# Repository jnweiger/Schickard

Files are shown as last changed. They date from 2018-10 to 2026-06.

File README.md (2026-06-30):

# Schickard
Lasercut reconstruction of the first calculating machine designed by Wilhelm Schickard 1623. 

Published at https://www.thingiverse.com/thing:3451695

Presented at
* <A href="https://www.facebook.com/pg/hackmake.de/events/">Hack-n-Make 2018</a>
* <A href="https://harenberg-maker.de/mmf-nuernberg-2019/">Mini Maker Faire Nürnberg (26. Jan 2019)</A>
* <a href="https://youtu.be/ot1D30ZgLgg">Make Munich 2019</a>
* <A HREF="http://www.VCFe.org/" TITLE="VCFe 20.0 am 27./28.April 2019 in München">VCFe 20.0 am 27./28.April 2019 in München VCFe 20.0 in München</A>
* <a href="http://www.faerdderla.de/events/modellbaunetzwerk-franken-5-modellbau-ausstellung-2/">5. Modellbau Ausstellung Franken (4./5. Mai 2019)</a>
* <a href="https://maker-faire.de/maker/die-schickardsche-rechenmaschine/">Maker Faire Berlin 2019 (17.-19.5.2019)</a>
* <a >Retrolution Hanau 2019</a>
* <a href="https://www.vcfb.de/2019/vortraege_workshops.html#schickard">Vintage Computer Festival Berlin 2019</a>
* <a href="https://www.lug-noris.de/lug-nuernberg/linux-presentation-day">Linux Presentation Day 2020.2</a>
* <a href="https://maischule.de/von-rechenmeistern-zur-rechenmaschine-eine-reise-in-die-vergangenheit-mit-juergen-weigert-vom-fab-lab-region-nuernberg-e-v">Maischule Fürth (10. Juli 2023)</a>
* <a href="https://meik.isc.schule/2026/06/15/schickardsche-rechenmaschine/">Industrieschule Chemnitz (15.6.2026)</a>

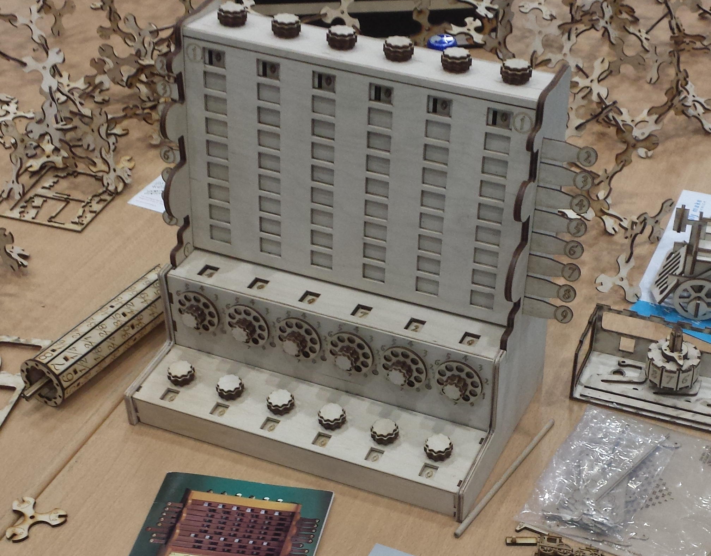
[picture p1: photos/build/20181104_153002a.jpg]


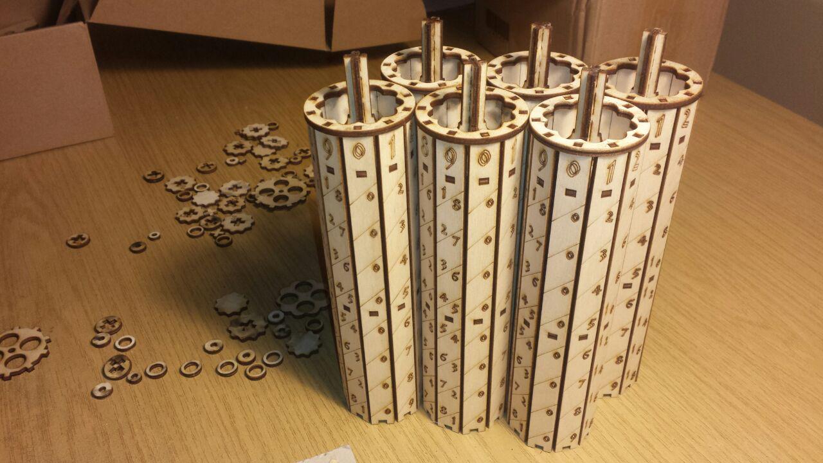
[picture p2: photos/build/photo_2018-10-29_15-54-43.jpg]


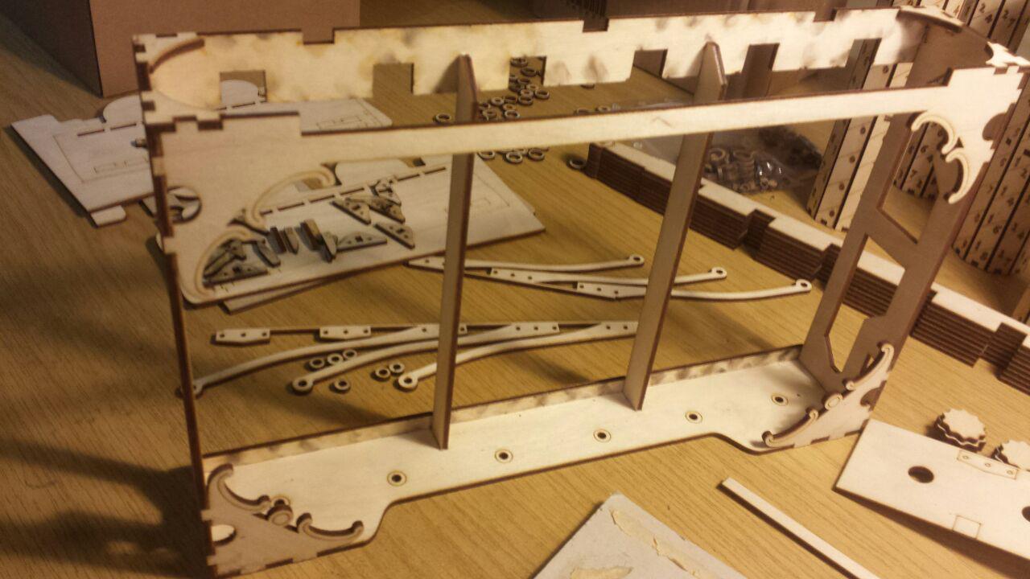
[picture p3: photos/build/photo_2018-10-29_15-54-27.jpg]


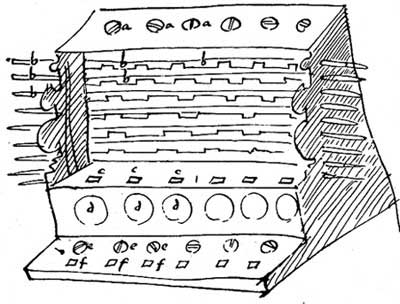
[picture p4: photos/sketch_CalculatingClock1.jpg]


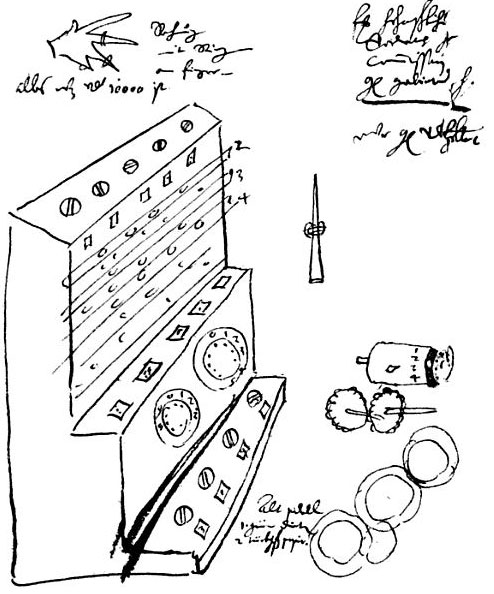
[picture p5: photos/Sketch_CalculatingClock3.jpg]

  
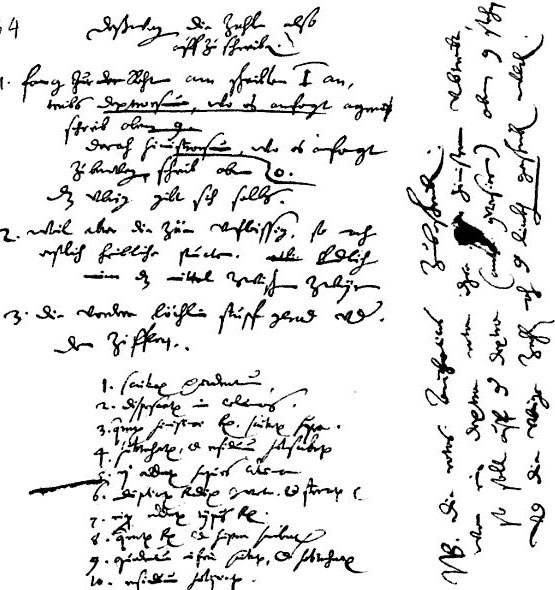
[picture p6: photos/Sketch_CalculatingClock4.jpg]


Video Clips:
* <a href="https://youtu.be/f-myRG2Cc5w">Test of the gear train</a>
* <a href="https://youtu.be/Xd8V1M9Gz_0">Adding 4+4+4+4 ...</a>
* <a href="https://youtu.be/RR3bb4ij2YE">Adding 753 + 296 = 1049</a>

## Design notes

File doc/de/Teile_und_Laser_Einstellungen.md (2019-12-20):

Beginne hier zu lesen.

Übersicht der Bauteile
======================

Die Teile der Maschine gliedern sich in fünf Gruppen:

* Speicherwerk (memory unit)
* Addierwerk (adder unit)
* Multiplikationswerk (napier unit)
* Seitenwände
* Übrige und optionale Teile

Die drei Werke und die Seitenwände sollten aus 3.2mm Birken-Sperrholz gefertigt werden.
Die Datei src/BOM.txt (billl of materials) listet alle benötigten Materialen.
Am wichtigsten davon sind drei Sperrholzplatten 76cm x 50cm. Aller lasergeschnittenen Teile
werden daraus gemacht.

Achte beim Holzeinkauf auf die exakte Dicke. Die Platten sollten maximal 3.2mm dick sein. Manche Hersteller verkaufen bis zu 3.5mm dicke Platten als 3mm (funktioniert hier nicht!). Manche Hersteller halten exakt 3.0mm ein (das funkioniert, baucht aber mehr Holzleim). Mit 3.2mm Holz funktionieren viele Verbindungen als stramme Steckverbindungen, die oft keinen Leim benötigen.
Birkensperrholz sollte in guter Qualität gekauft werden. Astfrei, glatt, absolut eben. Frage nach "Laserqualität". Mindestens handelsbezeichnung "BB/B".
Beim Zuschnitt muss die Holzmaserung in Längsrichtung verlaufen. (Holzfedern quer zur Maserung funktionieren nicht!)

Buchensperrholz ist auch eine gute Wahl. Es ist deutlich härter, aber auch teurer.
Billiges Pappelsperrholz sollte vermieden werden. Es ist zu weich für Zahnräder.

Die drei Dateien schickard_napiers.svg, schickard_adder.svg und schickard_memory.svg im Unterverzeichnis src ergeben die komplette Maschine. In jeder der Dateien sollte die Ebene 'laser' sichtbar sein. Dies ergibt einer 76cm x 50cm
Platte pro Datei.  Alle weiteren Dateien enthalten optionale Teile oder Hilfskonstruktionen aus denen die drei schickard_*.svg Dateien erzeugt wurden.

Im Folgenden wird beschrieben, was in den drei Platten enthalten ist. Die Teile sollten man streng nach Werken
sortiert werden. Du kannst die Platten nacheinander schneiden und zusammenbauen, wenn du dich an die Reihenfolge hier hältst. Das Multiplizierwerk (napier unit) wird zuletzt gebaut, da es die übrigbleibende Teile von den anderen Platten verwendet.

Speicherwerk
------------
Dieses Werk ist einfacher als die anderen, und sollte zuerst zusammengebaut werden.
Das Speicherwerk ist eine flache Kiste (ca. 33cm lang, 3cm hoch, 7cm tief) am unteren Ende der Maschine.
Auf der Oberseite sind sechs Drehknöpfe und sechs Fenster, die je eine Ziffer zeigen. Zu Beginn einer Multiplikation wird hier eine der beiden Zahlen durch die Drehknöpfe eingestellt.
Die Unterseite hat Aussparungen, um einen Blick in den Mechanismus zu erlauben.

Alle Teile des Speicherwerks finden auf der linken Hälfte der Datei schickard_memory.svg platz -- die rechte Hälfte enthält eine der Seitenwände und einige Teile des Multiplizierwerks.
Von einem Typ Ring sind 9 Exemplare vorhanden. Sechs davon werden für das Speicherwerk benötigt, drei gehören zum Multiplizierwerk.

Ausserdem befinden sich 13 Teile für Positionierhilfen auf der Platte, die nur während der Montage benutzt werden. Diese sind nicht Teil der Maschine.

 * Finde fünf kleine Rechtecke 32mm x 14mm mit gezahnten Aussparungen, die mit "Positioning Aid Knob Assembly" beschriftet sind. Weitere fünf dieser Teile sind unbeschriftet. (Nur je vier beschriftete und unbeschriftete werden benötigt. Falls eines verloren geht oder bricht, benutze das fünfte.)
 * Finde zwei gewinkelte Teile mit Innekurve ca. 6cm x 5cm mit der Beschriftung "Napier - Positioning Aid Side Connectors". Lege sie zur Seite, sie werden später bei den Seitenwänden benutzt.
 * Finde ein rechteckiges Teil ca. 7cm x 3cm mit der Beschriftung "Positioning Aid Side Connectors Memory". Lege es zur Seite, es wird später bei den Seitenwänden benutzt.

Addierwerk
----------
Das Addierwerk ist ein Kiste (ca. 33cm x 8cm x 8cm) in der Mitte der Maschine. Auf der Vorderseite sind sechs Räder mit Knöpfen. Jedes Rad hat 10 Löcher und kann mit einem 6mm Rundstab oder einem Stift bedient werden. Die Oberseite hat sechs Fensterchen, die das Rechenergebnis anzeigen.
Die  Kiste hat keinen Boden und die Rückseite ist durchbrochen, so dass der komplizierteste Teil der Maschine gut sichtbar ist: Das Räderwerk. Dieser Mechanismus dient dem Zehnerübertrag zur jeweils nächsten Stelle. [Wilhelm Schickard](https://en.wikipedia.org/wiki/Wilhelm_Schickard Wikipedia artikel über Wilhelm Schickard) war vermutlich der erste, der einen solchen Mechanismus konstruiert und gebaut hat.

Das Rechenergebnis wird in diesem Werk angezeigt. Um eine Multiplikation zu beginnen, sind die Räder so zu drehen, dass 000000 angezeigt wird.

Alle Teile passen in schickard_adder.svg und belegen etwa zwei Drittel einer Platte 76cm x 50cm. Das rechte Drittel dieser Datei enthält einen Satz Seitenwandteile und drei Sätze Kreuzwellen der Nepier-Walzen.

Ausserdem befinden sich 12 Teile für Positionierhilfen auf der Platte, die nur während der Montage benutzt werden. Diese sind nicht Teil der Maschine.

 * Finde fünf kleine Rechtecke 32mm x 14mm mit gezahnten Aussparungen, die mit "Positioning Aid Knob Assembly" beschriftet sind. Weitere fünf dieser Teile sind unbeschriftet. Es können statt dessen die Montagehilfen vom Speicherwerk auch hier verwendet werden. Dann werden diese 10 Teile nicht benötigt.
 * Finde zwei kleine Rechtecke ca. 11cm x 5cm, die mit "Positioning Aid Carry Wheels" beschriftet sind.

Alle Knöpfe sind gleich. Insgesamt werden 18 Stück benötigt.

Die Knöpfe des Addierwerks werden auf Lochscheiben montiert. Die Position der '0' ist mit einer kleinen Kerbe auf der Lochscheibe markiert.
Die Ziffernwalze wird aus einem verzahnten Ring, einer Scheibe und 10 Ziffernplätchen aufgebaut. Auf Ring und Scheibe ist die Position der '0' jeweils durch ein Rechteck markiert.
Die Wellen bestehen aus drei Teilen, die kreuzförmig verglebt werden. Es gibt zwei verschiedene Sätze Wellenteile, beschriftet "1, 100, 10.000" bzw. "10, 1.000, 100.000"
Alle Zahnräder und Abstandsquadrate werden von hinten auf die Wellen gesteckt. Die Schrift zeigt nach hinten.
Die grossen 10-Zähne-Räder haben die Position der '0' mit einem Strich markiert.

Die Reihenfolge der in der Teile auf die Wellen gesteckt werden, ist wie folgt:

3 Wellen "1, 100, 10.000":
  * erst 2x Einzahn,
  * dann 4x Abstandsquadrat,
  * dann 2x 10-Zähne-Rad aufstecken.

3 Wellen "10, 1.000, 100.000":
  * erst 2x 10-Zähne-Rad,
  * dann 4x Abstandsquadrat,
  * dann 2x Einzahn aufstecken.

Dabei sind die beiden Zahnstocherlöcher immer links. Mit den Zahnstochern
werden alle Teile genau ausgerichtet. Alle bis auf das letzte Teil werden ohne
Leim aufgesteckt, nur das letzte Teil und die beiden Zahnstocher werden
verklebt.

Die fünf Übertragswellen bestehen aus 6mm Buchenrundstäben, 90mm lang. Auf der
Rückwand sind sie mit A, B, C, D, E beschriftet.  Für bzw. A, C, E bzw. B, D
gibt es jeweils eine Montagehilfe "Positioning Aid Carry Wheels". Diese haben
passende Öffnungen für die Ringe und Räder.  Auch hier werden zwei Zahnstocher
zur genauen Ausrichtung montiert.  Mit dem letzten Ring wird die Welle in der
die Rückwand des Addierwerks befestigt, wie auf den Montagehilfe eingezeichnet.

Napier Unit
-----------
This is the upper part of the machine, where multiplications are done. It is named after [John Napier](https://en.wikipedia.org/wiki/John_Napier "Wikipedia Article on John Napier"), who invented the "[Napier's Bones](https://en.wikipedia.org/wiki/Napier%27s_bones)" giving the layout of the numbers on the drums.

The Napier unit consists of a box (ca. 33cm x 21cm x 6cm) with 6 drums standing upright. The back side of the box is open, to allow studying the interier,
the front has 8 sliders that can cover one row each of the multiplication table. Row "1" is always visible.
On the top are 6 knobs. To start multiplying, close all slides and enter one of the two numbers here by turing the knobs, so that it is shown in Row "1".

All parts for the box and most parts of the drums are in the schickard_napiers.svg file.
The layout fills one 76cm x 50 cm board. Two sets of napiers bones and several rings and shafts for the drums are
on the lower right hand side of the schickard_memory.svg. Three sets of shaft parts are on the right hand side
of schickard_adder.svg.

Side Walls
----------
The machine has a modular design. Each of the three units as its own enclosure. The left and right sides of the
machine are the two walls that hold the three modules in place. Each wall consits of two layer of plywood
 * the outer layer with only openings for the 8 slides,
 * the inner layer with openings for also the sides of the three units.

The memory unit is locked into the side walls using one connector on each side.
The napiers unit has two connectors (top and bottom) on each side.
The adder unit has none.

A wall connector is 30mm long, 6mm wide (two layers of plywood glued together), and in the middle 13mm high.
A rectanglar hole 4mm x 6mm goes across the connector.
Wall connectors are glued with their flat surface into the sidewalls. Their curved part extends into the sides of the memor or napier box. In this position a slim wedge can be inserted in to the hole of the connector locking the box in place.

Miscellaneous
-------------

The file schickard_misc_construction.svg has an additional set of rings (replacing the ones found in schickard_memory.svg). There are three different outer diameters 14.3mm, 14.4mm, and 14.5mm here. You can optionally cut these rings out of harder material like acrylic or kraftplex. The rings server as bearings for the shafts of napier and adder unit.

The file schickard_sign.svg has a wooden sign with two feet, for display with the machine. The sign is optional, it is not a part of the machine. This is designed for a 4mm plywood board.

There are also arrays of red lines, 90mm apart and 13mm apart. These can be used to cut the needed 4mm and 6mm
shafts from beech wood rods with a lasercutter.

Laser Settings
==============
To cut the parts from the boards you need access to a laser cutter with a bed of at least 76cm x 50cm size.
Find a machine large enough at your nearest FabLab or hacker space.
A machine with ca. 60-80 Watts is recommended. Expect ca. two hours cutting time and another two hours handling time
for collecting the parts from the machine and sort them into suitable containers. In total, there are ca. 600 parts.

The source files are are SVG format. These files can be processed with VisiCut (or converted with inkscape to PDF or other formats needed for your laser machine). Please re-check the dimensions (76 x 50) of the drawings after conversion.

The line colors (stroke or outline color) used in the SVG files have different meaning.

 * Red. These lines cut through the board. (E.g an 80W Thunderlaser may use speed 30, power 70/50 to cut through 3mm birchwood.)
 * Green. These lines are superficial markings. (E.g an 80W Thunderlaser may use speed 200, power 8/35 on birchwood.)
   Engraving mode (rasterization) may also work for green, but is not recommended, as it may be much slower.
 * Blue and other colors (if any) are to be ignored.

Several different fill colors were used during constructions, some parts have no fill.
These colors have no meaning for laser cutting.
Line width (stroke thickness) is typically 0.1 or 0.2mm. This also has no meaning for laser cutting.

Expect that some of the smaller parts may fall through the grid of the laser bed. It is recomended to clean any previous waste from the machine before starting. Most of the smaller parts come larger numbers than actually needed to save you from collecting each and every dropped piece.

A large table surface helps to keep the parts arranged into small piles. If needed, use containers like cardboard boxes or transparent zip bags for handling the parts between cutting and assembly.

Next steps
==========
Next read 'Adjustments and Maintenance' before assembly.
You learn there where to apply grease before a part becomes inaccessible.
Do not forget check out the assembly gallery in the photos folder before you start.

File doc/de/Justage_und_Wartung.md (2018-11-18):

Schmierung vor der Montage
==========================

Alle beweglichen Teile sollten mit Kerzenwachs eingerieben werden. Ein alter Kerzenstummel eignet 
sich gut dafür. Nimm Dir besonders Zeit, um

1) alle Flächen der kleinen Rollen an den Enden der Federn einzuwachsen.
2) alle Zähne von jedem Zahnrad einzuwachsen.

Die Schieber brauchen nur sehr wenig Schmierung. Sie dürfen etwas Reibung haben, da es keine Federn
gibt, um sie in Position zu halten.

Nach der Montage kann es sein, dass sich manche Knöpfe schwerer drehen lassen als andere, oder ungewöhnliche 
Geräusche machen. Du kannst dort nachträglich noch etwas Wachs aufbringen. Dazu kann es nötig sein, das Multiplikationswerk 
oder das Speicherwerk zu öffnen. Beim Addierwerk sollten alle Teile mit einer kleinen Messerspitze voll Wachs erreichbar sein.

Die Maschine soll keine schleifenden oder knarzenden Geräusche machen. Nur das Klicken der Federn, wenn eine Ziffer 
auf Position springt.

Justage des Addierwerks nach der Montage
========================================

Pro Rad gibt es einen langen Zahn, der in den linken Nachbar eingreift, um den Zehnerübertrag auszuführen.
Das passiert, wenn ein Rad im Uhrzeigersinn von 9 nach 0 gedreht wird (Addition) und auch, wenn ein Rad gegen
den Uhrzeigersinn von 0 nach 9 gedreht wird (Subtraktion).
Dieser Zahn greift nur zwischen 0 und 9 ein. In den Positionen 0 und 9 muss der Zahn ausser Eingriff sein.
Das Rad links daneben muss sich besonders in diesen beiden Fällen frei frei drehen lassen.

Um diese Einstellung zu erreichen, kann die Holzfeder hinten im Addierwerk seitlich um ca 2mm verschoben werden.

1) Beginne mit der Feder in Mittelposition, so dass links und rechts 1 mm Weg frei sind.
2) Verstelle die Räder des Addierwerks, bis die Anzeige 9 9 9 9 9 9 zeigt.
3) Drehe die Maschine um, und suche die langen Zähne im addierwerk.
4) Von hinten gesehen, sollten die langen Zähne jeweils nach südost zeigen und sollten vom benachbarten Zahnrad 
   ca 0.5mm Abstand haben. Den Spalt kann man am besten sehen, wenn man von unten ins Addierwerk blickt.
   Schneide schmalen Streifen von einer Visitenkarte, dieser sollte leicht zwischen Zahn und Zahnrad
   passen.
5) Falls die Zähne zu weit von den Zahnrädern entfernt sind, verschiebe die Feder um ein paar Zehntel Millimeter 
   nach links. Der Spalt wird enger.
6) Falls die Zähne das Zahnrad berühren oder sogar eingreifen, schiebe die Feder nach rechts, bis ein Spalt entsteht.
7) Verstelle die Räder des Addierwerks, bis die Anzeige 0 0 0 0 0 0 zeigt.
   Falls die Maschine perfekt eingestellt ist, kann dies erreicht werden, in dem du nur das ganz rechte Rad (Einerstelle)
   im Uhrzeigersinn drehst. Alle Räder drehen sich mit.
   Am Anfang kann das sehr schwer gehen. Drehe das Rad der Einerstelle nur soweit nach rechts, bis sich die Zehner, Hunderter und 
   Tausenderstelle ein wenig bewegen. Dann greife mit der anderen Hand in die Tausernderstelle und helfe ein wenig mit, so dass sich 
   die Einerstelle leichter weiterdrehen lässt. Falls das funktioniert, ist die Maschine 'gut genug' justiert.
   Falls der Mechanismus blockiert, drehe jedes Rad entgegen dem Uhrzeigersinn, über alle Stellen zurück von 9 bis 0.
8) Drehe die Maschine wieder um, und suche die langen Zähne. Sie sind jetzt weiter oben im Getriebe und zeigen nach Ostsüdost.
9) Alle langen Zähne sollten nun wieder ausser Eingriff sein. Der Spalt sollte genauso breit sein, wie im ersten Fall.
10) Falls nötig verstelle die Feder. Dann fixiere sie mit etwas Leim an den Stiften in der besten Position.
11) Falls es keine Postion gibt, in der alle langen Zähne gleichzeitig und in beiden Positionen (0 und 9) frei sind,
   kannst du eine kleine Schlüsselfeile verwenden, um vorsichtig etwas Material von den betreffenden Zähnen abzutragen.

Alle Räder sollten sich nun frei drehen lassen, unabhängig von der Stellung ihrere Nachbarn.
Während einer Addition sollte niemals ein Rad blockierne. Dies darf gelegentlich bei einer Subtraktion passieren, wenn der rechte
Nachbar 0 zeigt. Du kannst das Rad frei bekommen, indem du den rechten Nachbar ein klein wenig gegenhälst.
Falls das öfter passiert, solltest du die Einstellung der Feder erneut nach obiger Prozedur überprüfen. 
Die Holzkonstruktion reagiert auf Temperaturschwankungen und Feuchtigkeit, und wird nach einiger Zeit etwas mehr Spiel haben.

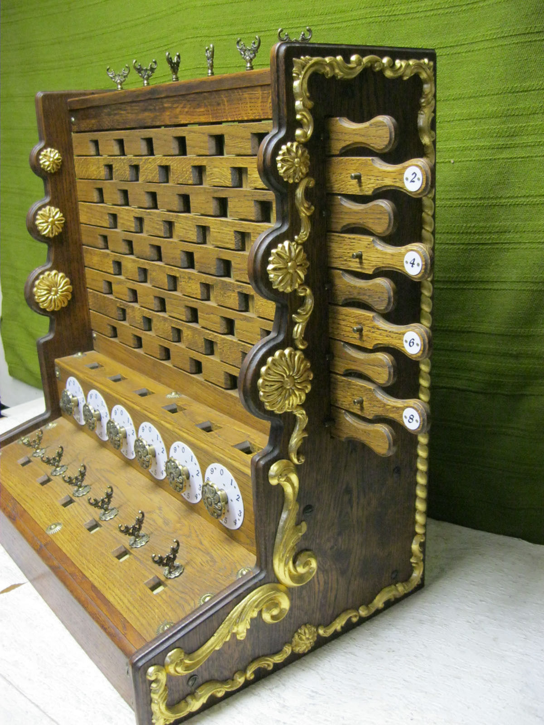
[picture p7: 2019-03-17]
photos/expensive_design_1.jpg

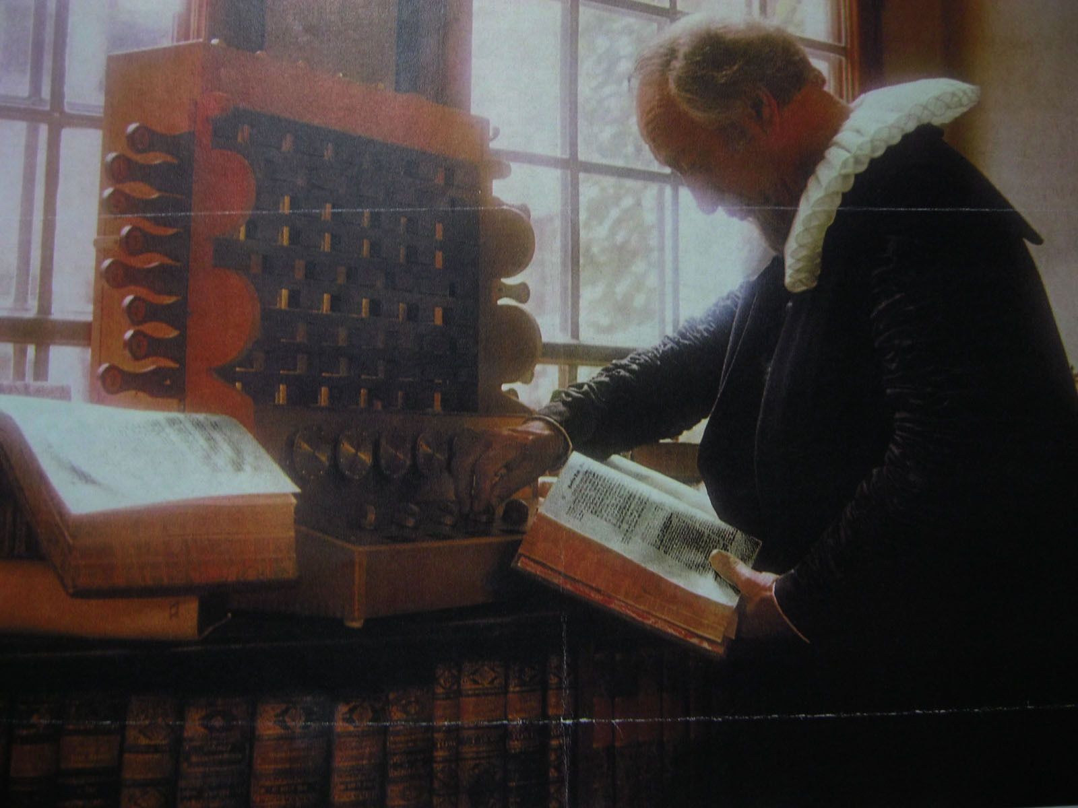
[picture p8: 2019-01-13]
photos/expensive_design_3.jpg

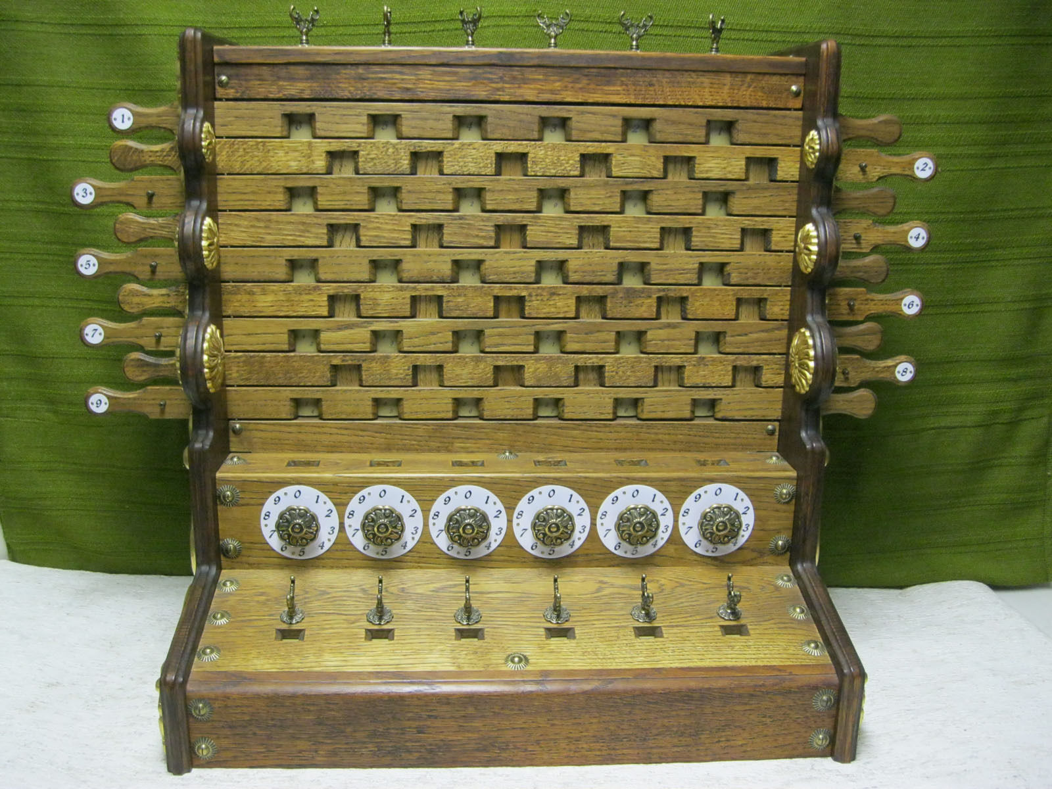
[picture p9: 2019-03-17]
photos/expensive_design_2.jpg

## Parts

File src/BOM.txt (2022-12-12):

Everything is made from wood. Assembly takes several days, and requires some 
skill, passion for precision, and patience.

The estimated lasercutter time is 3 to 4 hours (including handling).
The smaller parts are included in double or triple quantities, often with 
indicated size variants, to accomodate laser kerf and exact thickness of the plywood.
The 14mm rings for the adder box can be made from 3mm Kraftplex for better quality.

Shopping list
=============
 - Either
    - 3x plywood 50cm x 76cm, 3.2mm (e.g. https://www.ebay.de/itm/Sperrholzplatten-3mm-Birke-10-90-m-Bastelholz-Holzplatte-Modellbau-Sperrholz/251233553554)
    - plywood ca 22cm x 20cm, 4mm (for the sign)
   or
    - 10x plywwood 50 cm x 30 cm, 3.2mm (see subfolder 50x30, this includes the sign in 3mm thickness)
 - optionally 3mm Kraftplex ca 9cm x 15cm for extra strong 10mm rings as bearings.
 - 5x beechwood cylindrical rod, 6mm diameter, 90mm (buy 1m, cut yourself)
 - 26x beechwood cylindrical rod, 4mm diameter, 13mm (buy 1m, cut yourself)
 - ca 100 toothpics, 2mm diameter.
 - wood glue (e.g. Bindan Propellerleim, Ponal Express)
 - candlestump 
 - sandpaper grain 180
 - adhesive tape (e.g. painters tape)

Tools
=====
 - Flat surface, cardboard (to collect dust, broken toothpicks, excess glue, etc.
 - Lasercutter, large enough for the boards (e.g. a Thunderlaser Nova35 at your nearby FabLab)
 - Small and large plastic bags with zip (to collect all the pieces)
 - Pliers
 - File

Software
========
 - inkscape (open the SVG file, select laser layers)
 - VisiCut (or whatever is needed to drive the laser)

Parts count
===========

Total: 132+61+14+174+40+50+60+44 = 577

Neper drums
-----------
 6 x 22 = 132

Neper box
---------
  6*(3+1) + 3+2+3+2+4+8+4+8+2+1 = 61 
  3*(3+1) + 2 = 14

Adder wheels and drums
----------------------
  6*(7+5+12+5) = 174
  5*(1+2+5) = 40

Adder box
---------
  6*(2+1+2) + 6+6+4+4 = 50
 
Memory wheels and disks
-----------------------
  6*(4+3+2+1) = 60

Memory box
----------
  6*(1+3) + 5+6+1+2+4+2 = 44

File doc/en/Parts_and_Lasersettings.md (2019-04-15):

Read this first.

Parts Overview
==============

The parts of the machine are organized in 5 groups:

* Memory unit
* Adder unit
* Napier unit
* Side walls
* Miscellaneous and optional parts

The three units and the side walls should be made from 3.2mm birch plywood.
The bill of materials src/BOM.txt lists all needed raw material.
Most important are three boards of plywood 76cm x 50cm. All lasercut parts are made from these.

When buying the wood, please make sure it is max 3.2mm thick. Some vendors sell up to 3.5mm thick boards when asked for 3mm (this will not work!). Other vendors can do exact 3.0mm (this works, but needs much glue). With 3.2mm many connections are nice press fits, and need very little glue.
Birch is available in good qualities. You want no gnarls or knots, but smooth and perfectly flat boards.
Ask for "laser quality". The grain must run parallel to the long side of the boards. (Wodden springs do not work when cut crosswise to the grain!)

Beech is also a good choice. It is much harder, but also more expensive.
Do not use inexpensive poplar or cottonwood. It is too soft for cutting gears.

Lasercut the three files schickard_napiers.svg, schickard_adder.svg and schickard_memory.svg found in the src folder.
In each of these, a layer named 'laser' should be visible, representing one board 76cm x 50cm each. These three boards represent the entire machine. All other files are optional or contain construction sketches that were used to produced the three schickard_*.svg files.

The following is a description what is contained in these boards. It is best to keep the parts well sorted according to the unit they belong to. You can lasercut one board at a time and assemble one unit of the machine, if you start in the order given here. Do the napier unit last, it needs all the parts left over from the other two boards.

Memory Unit
-----------
This unit is the simplest of all, it should be assembled first.
The memory unit is a flat box (ca. 33cm long, 3cm high, 7cm deep) at the bottom of the machine.
The top surface of the box has six knobs and six windows showing one digit each. To start multiplying, enter
one of the two number here by turning the knobs.
The bottom of the box as some openings to allow viewing the interior mechanism.

All parts of the memory unit are found on the left hand side of the file
schickard_memory.svg -- the right hand side of this 76cm x 50cm board contains one of the
side walls, and several parts for the napier unit.
Of one type of ring, there are 9 copies. Six are used for the memory unit, three belong to the napier unit.

Also in this board are 13 parts for positioning aids used during assembly. They are not part of the machine.

 * Locate five small 32mm x 14mm rectangles with a toothed cut out. They are labeled "Positioning Aid Knob Assembly". There are five more unlabled parts very similar to the labeled ones. (Only four of each are needed, there are five incase you break or loose one.)
 * Locate two angled pieces with an inner curve ca. 6cm x 5cm. They are labeled "Napier - Positioning Aid Side Connectors". Put them aside, they are used later when assembling the side walls.
 * Locate one rectanglare piece ca. 7cm x 3cm. It is labeled "Positioning Aid Side Connectors Memory". Put it aside, it is used later when assembling the side walls.

Also on this board are two sets of rings.
The set on the bottom edge has 14.4mm outer diameter, the set on the right hand edge has 14.3mm. Use the set that fits best, discard the other. Optionally use rings from a stronger material like e.g. Kraftplex.
Put them aside, they are used later with the adder and napier units.

Adder Unit
----------
The adder unit is a box (ca. 33cm x 8cm x 8cm) in the center of the machine. It has six wheels with knobs on its front, each wheel has 10 holes that can be operated with a 6mm rod or the end of a pen.
The top surface features six windows, where the result is displayed.
The box has no bottom and the back wall has many openings to allow a good view on the most complex part of the machine: the gears. This mechanism performs correct carry-over to neigbouring digits.
[Wilhelm Schickard](https://en.wikipedia.org/wiki/Wilhelm_Schickard) was most likely the first to design and document such a mechanism.

The result of all computations are displayed in this unit. To start multiplying, turn the wheels so that 000000 is displayed.

All parts fit on schickard_adder.svg using ca. two third of a 76 x 50 board. The right hand third of this file contains one set of side wall parts, and three sets of shafts for the napier drums.

Also on this board are 12 parts that positioning aids used during assembly. They are not part of the machine.

* Locate five small 32mm x 14mm rectangles with a toothed cut out. They are labeled "Positioning Aid Knob Assembly". There are five more unlabled parts very similar to the labeled ones. You can re-use the knob assembly aids from the memory unit and discard these 10 parts found here.
* Locate two rectangles ca 11cm x 5cm labeled "Positioning Aid Carry Wheels".

All knobs are identical. We need a total of 18 knobs.

The knobs for the adder unit are mounted on 10-hole disks. The disks have the '0' position marked with a small notch.
The digit drums consist of one toothed ring, a disk and 10 number-pads. Ring and disk have their '0' position marked with a rectangle.
The shafts are composed of three parts, glued together to form a cross. There are two sets of shaft parts, labeled "1, 100, 10.000" and "10, 1.000, 100.000"
All gears and spacer squares are pushed onto the shafts from the rear end. The labels face rear.
The large 10-tooth-gears have their '0' position marked with a line.

Parts are pushed onto the shafts in the following order:

3 shafts "1, 100, 10.000":
  * first 2x one-tooth,
  * then 4x spacer square,
  * then 2x 10-tooth-gear.

3 shafts "10, 1.000, 100.000":
  * first 2x 10-tooth-gear,
  * then 4x spacer square,
  * then 2x one-tooth.

Each of these parts has two holes for toothpicks. These holes face to the left
and are toothpicks are used to align the parts precisely. All but the last part
are mounted without glue. Only the two toohtpicks and the last part are glued.

The five carry shafts are 6mm diameter beechwood, 90mm long. The back wall
lables them A, B, C, D, E.  For A, C, E and B, D respectively find a
"Positioning Aid Carry Wheels". The openings fit the wheels or rings for each
position.  Two toothpicks are used here too for precise alignment.  The last
ring mounts the shaft into the back wall of the adder unit, as indicated on the
positioning aids.

Napier Unit
-----------
This is the upper part of the machine, where multiplications are done. It is named after [John Napier](https://en.wikipedia.org/wiki/John_Napier "Wikipedia Article on John Napier"), who invented the "[Napier's Bones](https://en.wikipedia.org/wiki/Napier%27s_bones)" giving the layout of the numbers on the drums.

The Napier unit consists of a box (ca. 33cm x 21cm x 6cm) with 6 drums standing upright. The back side of the box is open, to allow studying the interier,
the front has 8 sliders that can cover one row each of the multiplication table. Row "1" is always visible.
On the top are 6 knobs. To start multiplying, close all slides and enter one of the two numbers here by turing the knobs, so that it is shown in Row "1".

All parts for the box and most parts of the drums are in the schickard_napiers.svg file.
The layout fills one 76cm x 50 cm board. Two sets of napiers bones and several rings and shafts for the drums are
on the lower right hand side of the schickard_memory.svg. Three sets of shaft parts are on the right hand side
of schickard_adder.svg.

Side Walls
----------
The machine has a modular design. Each of the three units as its own enclosure. The left and right sides of the
machine are the two walls that hold the three modules in place. Each wall consits of two layer of plywood
 * the outer layer with only openings for the 8 slides,
 * the inner layer with openings for also the sides of the three units.

The memory unit is locked into the side walls using one connector on each side.
The napiers unit has two connectors (top and bottom) on each side.
The adder unit has none.

A wall connector is 30mm long, 6mm wide (two layers of plywood glued together), and in the middle 13mm high.
A rectanglar hole 4mm x 6mm goes across the connector.
Wall connectors are glued with their flat surface into the sidewalls. Their curved part extends into the sides of the memor or napier box. In this position a slim wedge can be inserted in to the hole of the connector locking the box in place.

Miscellaneous
-------------

The file schickard_misc_construction.svg has an additional set of rings (replacing the ones found in schickard_memory.svg). There are three different outer diameters 14.3mm, 14.4mm, and 14.5mm here. You can optionally cut these rings out of harder material like acrylic or kraftplex. The rings server as bearings for the shafts of napier and adder unit.

The file schickard_sign.svg has a wooden sign with two feet, for display with the machine. The sign is optional, it is not a part of the machine. This is designed for a 4mm plywood board. The SVG file has multiple layers. You can
select english and german text by disabling/enabling layers using inkscape.

There are also arrays of red lines, 90mm apart and 13mm apart. These can be used to cut the needed 4mm and 6mm
shafts from beech wood rods with a lasercutter.

Laser Settings
==============
To cut the parts from the boards you need access to a laser cutter with a bed of at least 76cm x 50cm size.
Find a machine large enough at your nearest FabLab or hacker space.
A machine with ca. 60-80 Watts is recommended. Expect ca. two hours cutting time and another two hours handling time
for collecting the parts from the machine and sort them into suitable containers. In total, there are ca. 600 parts.

The source files are are SVG format. These files can be processed with VisiCut (or converted with inkscape to PDF or other formats needed for your laser machine). Please re-check the dimensions (76 x 50) of the drawings after conversion.

The line colors (stroke or outline color) used in the SVG files have different meaning.

 * Red. These lines cut through the board. (E.g an 80W Thunderlaser may use speed 30, power 70/50 to cut through 3mm birchwood.)
 * Green. These lines are superficial markings. (E.g an 80W Thunderlaser may use speed 200, power 8/35 on birchwood.)
   Engraving mode (rasterization) may also work for green, but is not recommended, as it may be much slower.
 * Blue and other colors (if any) are to be ignored.

Several different fill colors were used during constructions, some parts have no fill.
These colors have no meaning for laser cutting.
Line width (stroke thickness) is typically 0.1 or 0.2mm. This also has no meaning for laser cutting.

Expect that some of the smaller parts may fall through the grid of the laser bed. It is recomended to clean any previous waste from the machine before starting. Most of the smaller parts come larger numbers than actually needed to save you from collecting each and every dropped piece.

A large table surface helps to keep the parts arranged into small piles. If needed, use containers like cardboard boxes or transparent zip bags for handling the parts between cutting and assembly.

Next steps
==========
Next read 'Adjustments and Maintenance' before assembly.
You learn there where to apply grease before a part becomes inaccessible.
Do not forget check out the assembly gallery in the photos folder before you start.

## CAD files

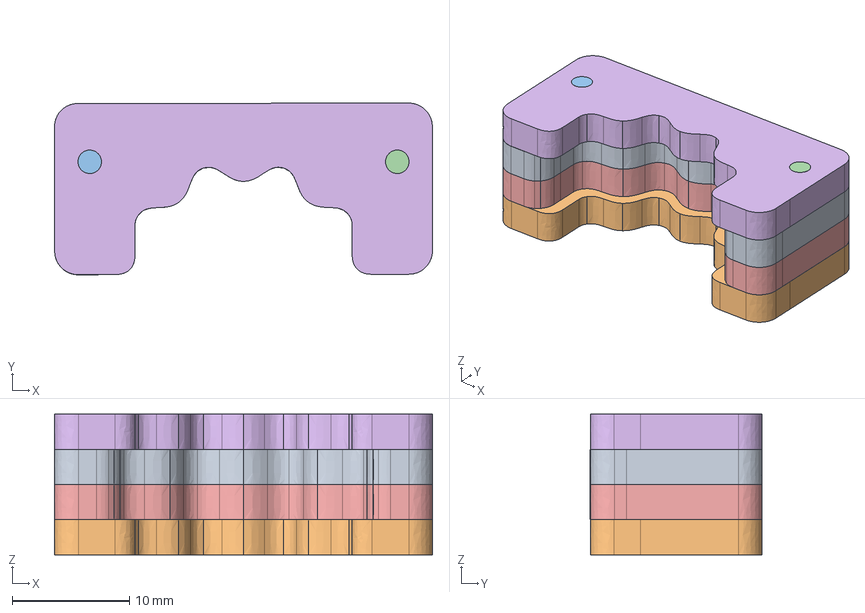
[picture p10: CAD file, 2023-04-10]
src/freecad/knob_assembly_positioning_aid.FCStd
32.2 x 14.6 x 12.0 mm
Inner
Outer
Toothpick
Toothpick001
Inner001
Outer001

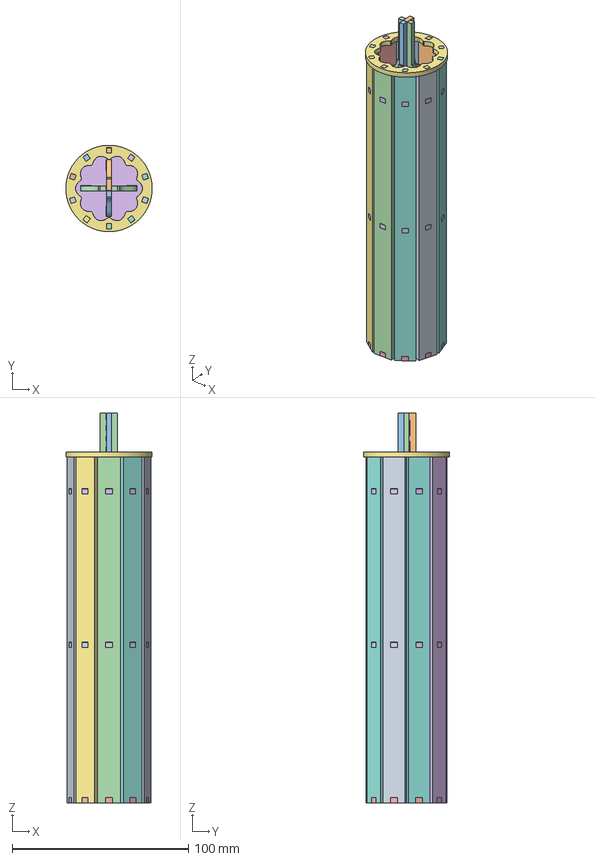
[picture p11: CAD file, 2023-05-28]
src/freecad/napier_drums.FCStd
49.0 x 49.0 x 221.0 mm

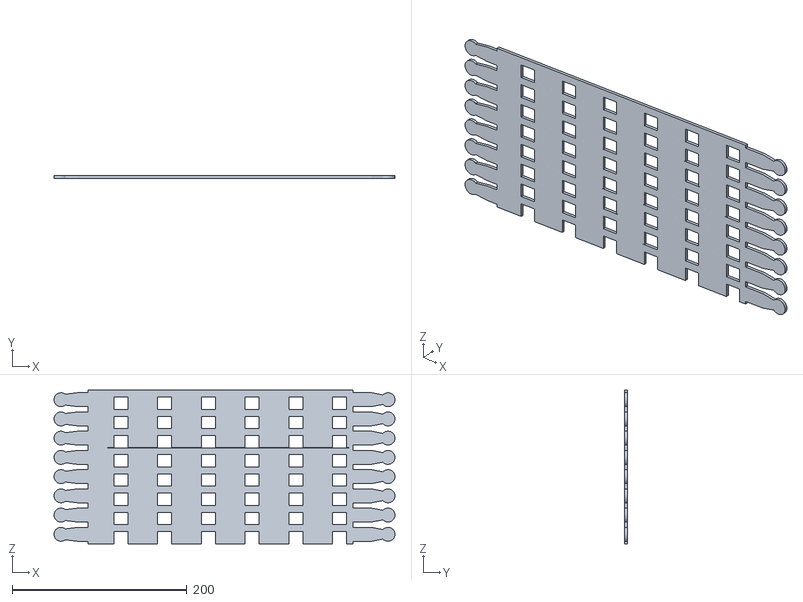
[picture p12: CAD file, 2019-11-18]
src/freecad/stl/napier_sliders.stl
390.0 x 3.00 x 176.0

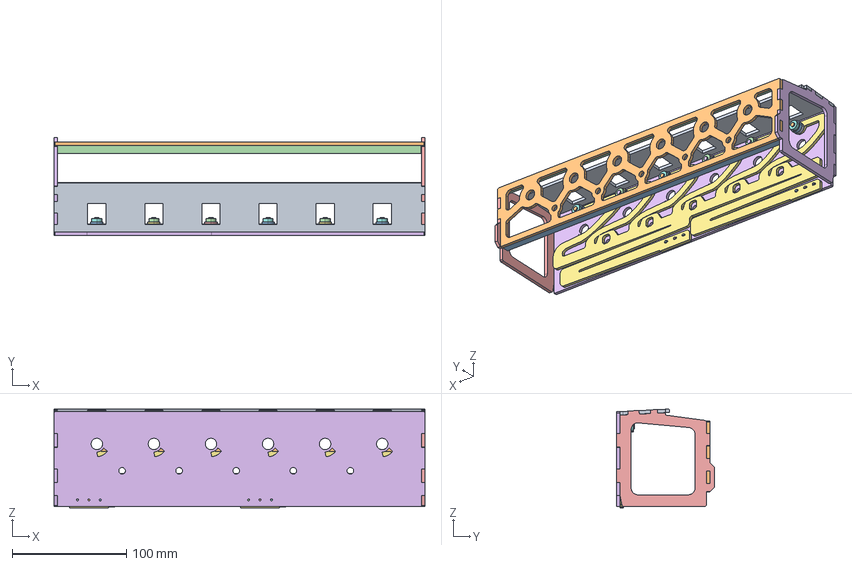
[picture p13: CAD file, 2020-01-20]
src/freecad/adder_box.FCStd
325.0 x 86.2 x 86.7 mm
Top
Spring
Roller_8_4
Roller_11_4_2
Pin_4
Roller_11_4
Roller_8_010
Roller_11_010
Pin_010
Roller_11_4_003
Roller_8_006
Roller_11_006
Pin_006
Roller_11_011
Roller_8_007
Roller_11_007
Pin_007
Roller_11_012
Roller_8_008
Roller_11_008
Pin_008
Roller_11_013
Roller_8_009
Roller_11_009
Pin_009
Roller_11_014
Pin_2

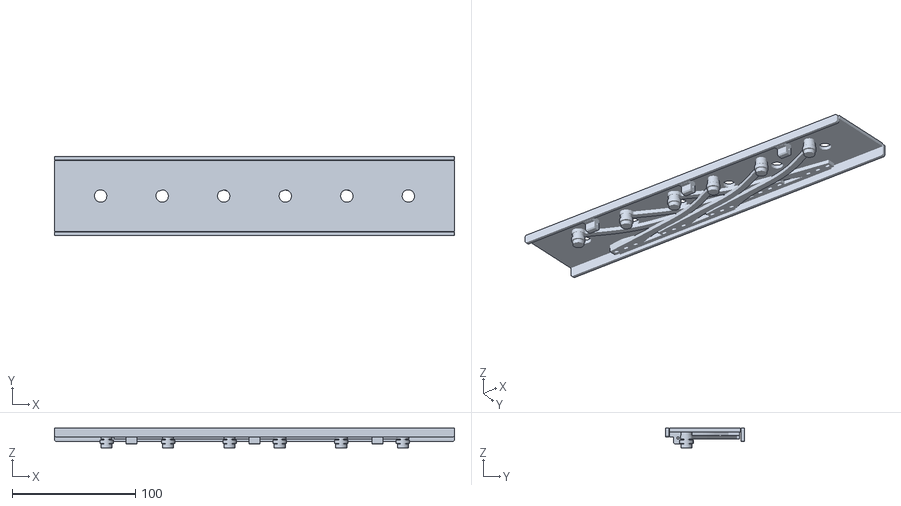
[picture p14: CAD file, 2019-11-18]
src/freecad/stl/napier_lid.stl
325.0 x 64.2 x 16.0

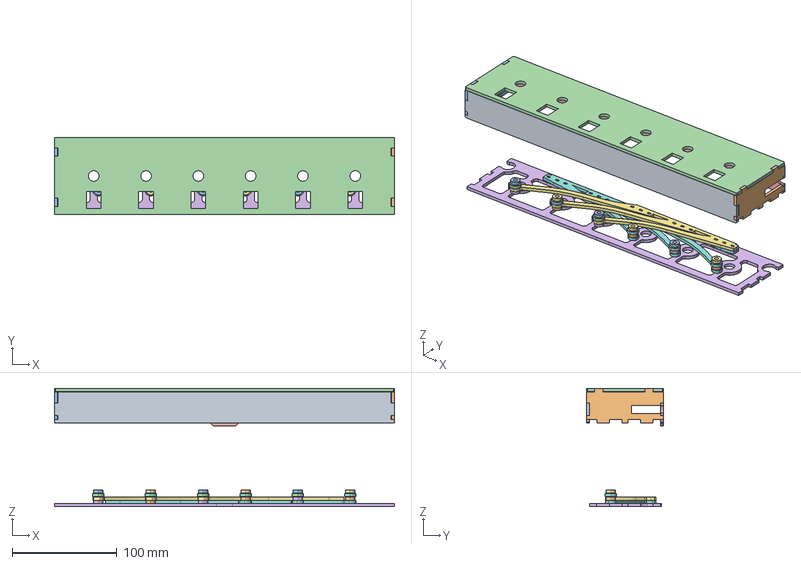
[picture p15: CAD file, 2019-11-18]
src/freecad/memory_box.FCStd
325.0 x 74.0 x 112.9 mm
front
right
left001
top001
back
bottom001
Roller_8_4_
Roller_11_4_
Pin_4
Roller_8_4_005
Roller_8_4_006
Roller_11_4_001
Pin_005
Roller_8_4_007
Roller_8_4_008
Roller_11_4_002
Pin_006
Roller_8_4_009
Roller_8_4_010
Roller_11_4_003
Pin_007
Roller_8_4_011
Roller_8_4_012
Roller_11_4_004
Pin_008
Roller_8_4_013
Roller_8_4_014
Roller_11_4_005
Pin_009
Roller_8_4_015
spring_2_
spring_1_

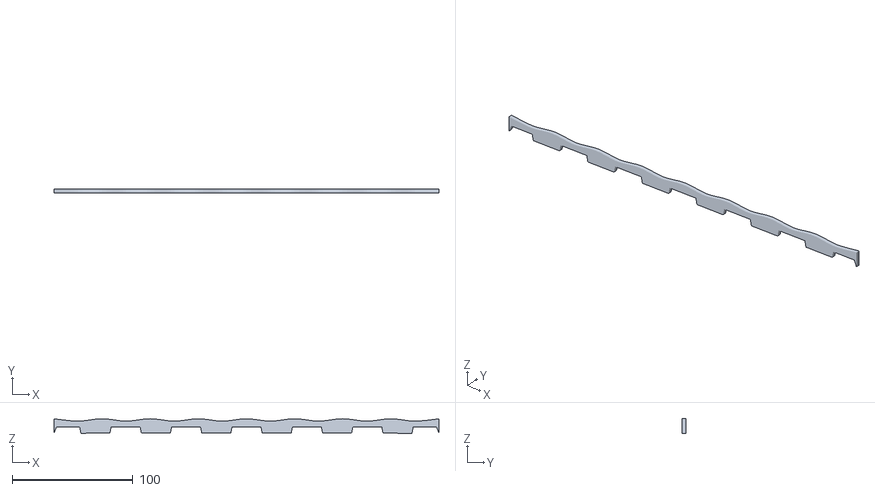
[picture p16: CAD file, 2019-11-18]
src/freecad/stl/napier_blinds_pos_aid.stl
318.6 x 3.00 x 12.0

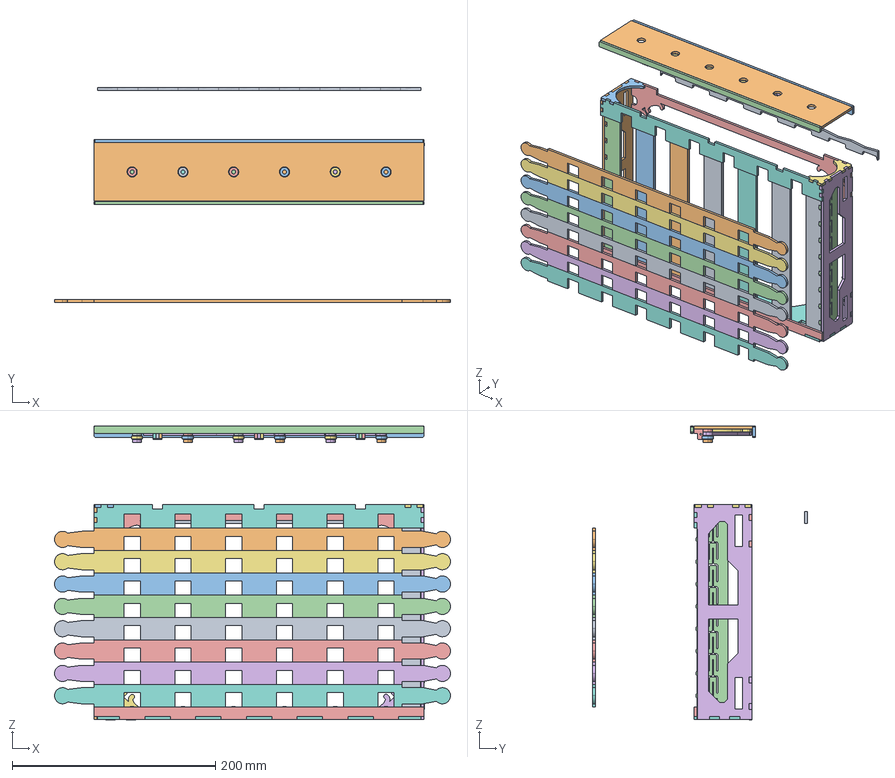
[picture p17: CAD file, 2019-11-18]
src/freecad/napier_box.FCStd
390.0 x 211.5 x 289.2 mm
lid_back
lid_front
lid_hook
lid_hook001
lid_hook002
lid_hook003
lid_hook004
lid_hook005
lid_hook006
lid_hook007
lid_hook008
Roller_8_4_
Roller_11_4_
Pin_4
Roller_8_4_005
Roller_8_4_006
Roller_11_4_001
Pin_005
Roller_8_4_007
Roller_8_4_008
Roller_11_4_002
Pin_006
Roller_8_4_009
Roller_8_4_010
Roller_11_4_003
Pin_007
Roller_8_4_011
Roller_8_4_012
Roller_11_4_004
Pin_008
Roller_8_4_013
Roller_8_4_014
Roller_11_4_005
Pin_009
Roller_8_4_015
spring_2_
spring_1_
blind001
blind002
blind003
blind004
slider_spring
blind
top_left
blind_side
front_bottom
top_right
blind_side001
Pin_010
Roller_8_4_016
Pin_011
Roller_8_4_017
Pin_012
Roller_8_4_018
Pin_013
Roller_8_4_019
Pin_014
Roller_8_4_020
Pin_015
Roller_8_4_021

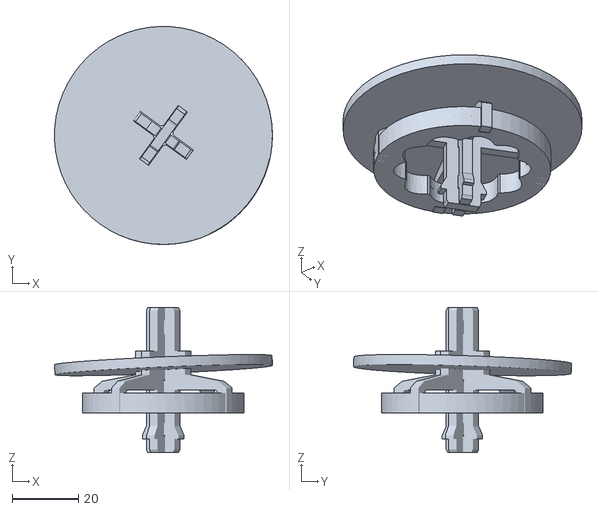
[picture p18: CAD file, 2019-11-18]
src/freecad/stl/memory_wheel.stl
66.0 x 66.0 x 44.0

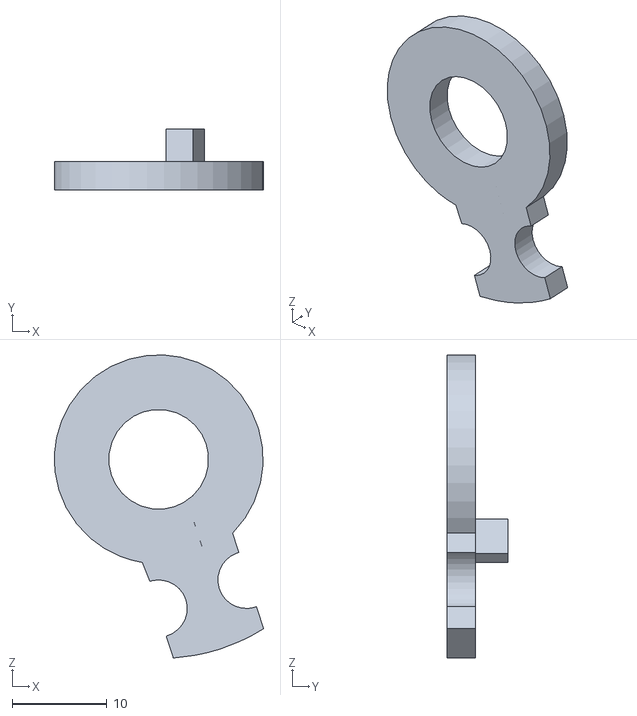
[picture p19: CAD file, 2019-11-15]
src/freecad/stl/adder_wheels_pendulum.stl
22.0 x 6.40 x 31.9

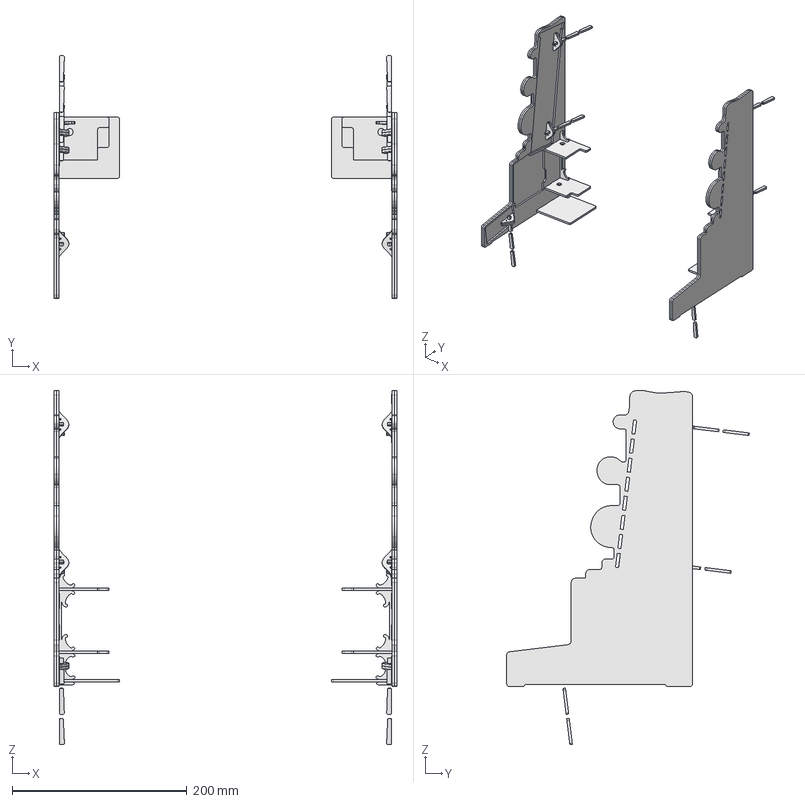
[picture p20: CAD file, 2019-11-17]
src/freecad/side_walls.FCStd
393.0 x 278.1 x 406.1 mm
Wall_Connector007
Wall_Connector008
Wall_Connector009
Wall_Connector010
Wall_Connector011
Wall_Connector012
Wall_Connector
Wall_Connector001
Wall_Connector002
Wall_Connector003
Wall_Connector005
Wall_Connector006
circle136845 x 2
circle136847 x 2
circle136855 x 2
circle136857 x 2
circle136729 x 2
circle136731 x 2
circle136739 x 2
circle136741 x 2

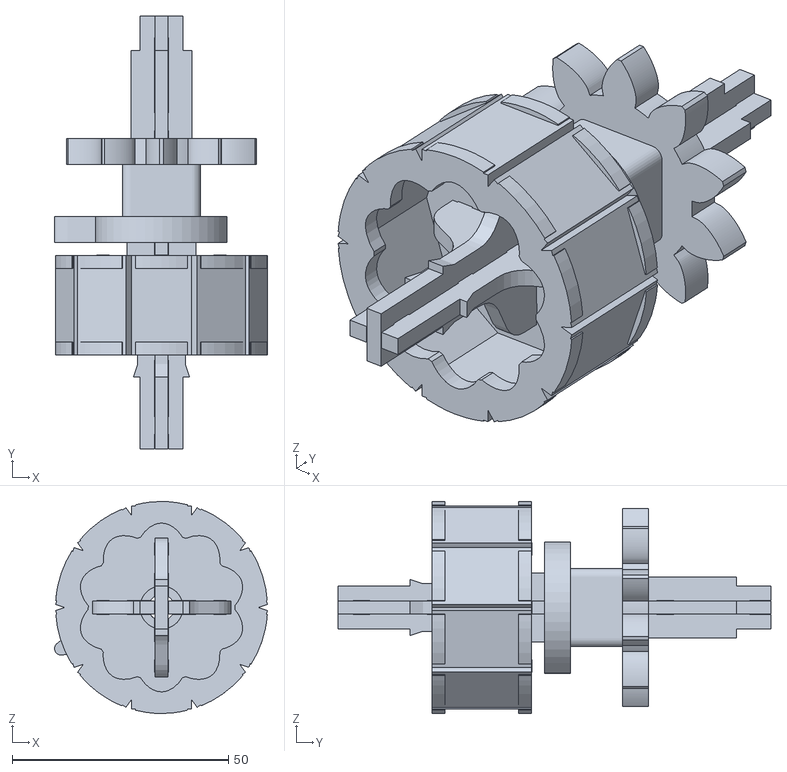
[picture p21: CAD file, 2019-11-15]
src/freecad/stl/adder_wheels_shaft_1_100_10.000.stl
49.2 x 100.0 x 49.0

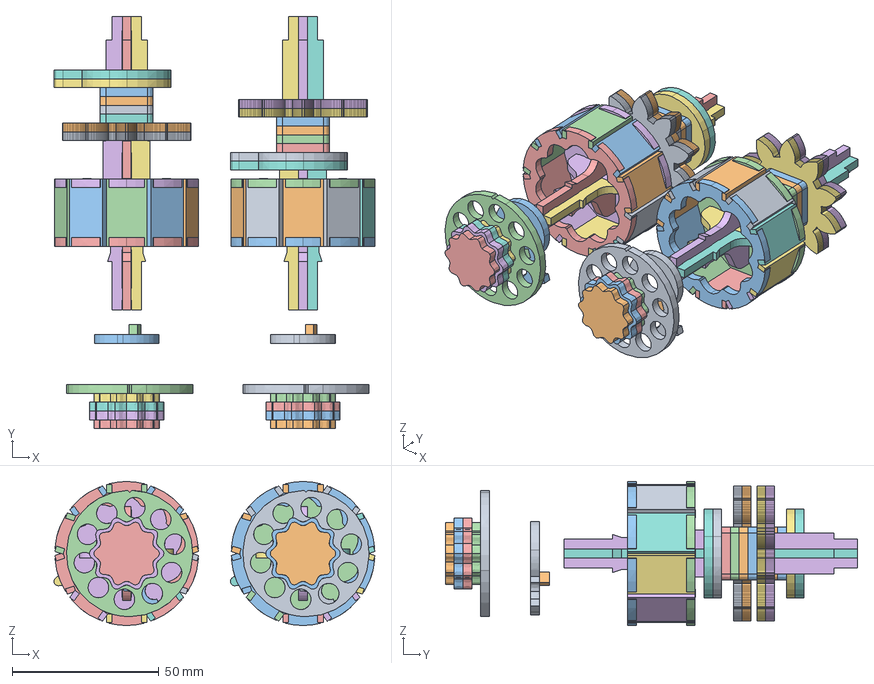
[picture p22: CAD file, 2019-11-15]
src/freecad/adder_wheels.FCStd
109.2 x 140.3 x 49.0 mm
front_wheel
knob_1
distance
distance002
distance003
distance004
distance001
distance005
distance006
distance007
front_wheel001
knob_007
pendulum
pendulum_stop
pendulum001
pendulum_stop001

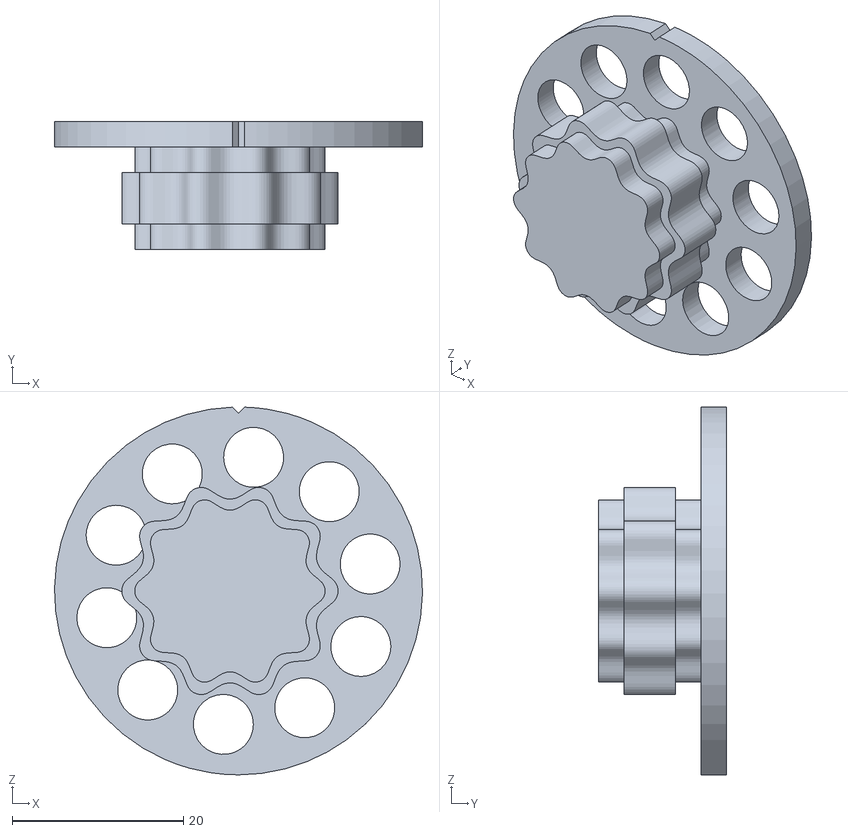
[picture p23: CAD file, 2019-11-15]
src/freecad/stl/adder_wheels_front_knob.stl
43.0 x 15.0 x 43.0

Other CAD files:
src/freecad/stl/napier_drum.stl
src/freecad/memory_wheels.FCStd
src/freecad/adder_carry.FCStd
src/freecad/stl/adder_carry_with_aids.stl
src/freecad/sign.FCStd
src/freecad/stl/adder_box.stl
src/freecad/stl/adder_carry_A_C_E.stl
src/freecad/stl/adder_carry_B_D.stl
src/freecad/stl/adder_wheels.stl
src/freecad/stl/napier_box.stl
src/freecad/stl/side_walls.stl

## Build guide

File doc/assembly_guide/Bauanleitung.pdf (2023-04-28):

2023-04-26, jw

## Bauanleitung Schickard’sche Rechenmaschine

Konstruktion Jürgen Weigert - 2018 - thingiverse.com/thing:3451695

## 1. Material und Werkzeug

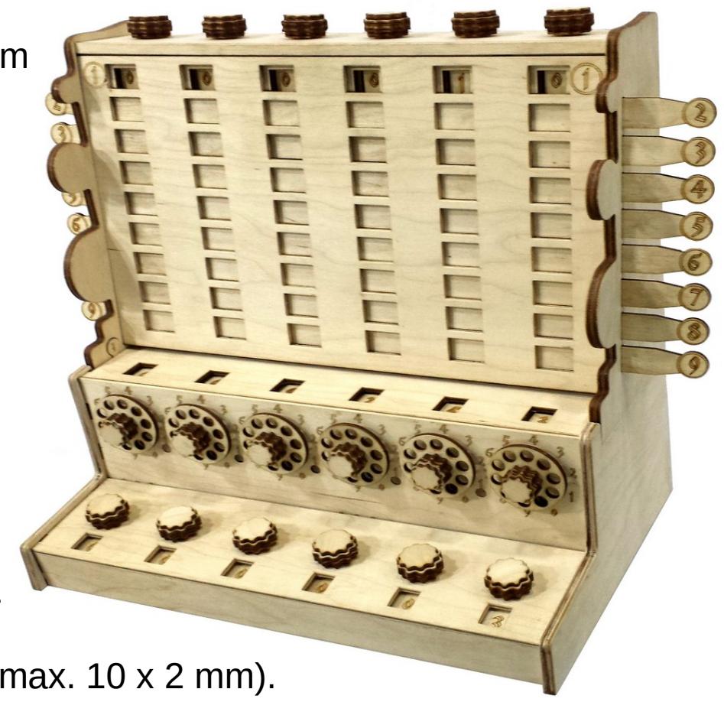
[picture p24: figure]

- Lasercut Bausatz Birkensperrholz 3.2 mm
- Arbeitstisch, groß.
- Kreppklebeband
- viele Wäscheklammern
- Spitzzange
- Kerzenstummel
- Schleifpapier Körnung 180
- Sortierhilfen (Schalen, Plastikbeutel)
- ca. 50 Zahnstocher, 2 mm Durchmesser
- kleine Feilen, rund (< 4 mm ) und flach (max. 10 x 2 mm).
- Weißer Holzleim (Bindulin Propellerleim, Ponal Express, …)

## 2. Übersicht Baugruppen

Die Teile der Maschine gliedern sich in fünf Gruppen:
- Speicherwerk (memory unit)
- Addierwerk (adder unit)
- Multiplikationswerk (napier unit)
- Seitenwände
- Schild

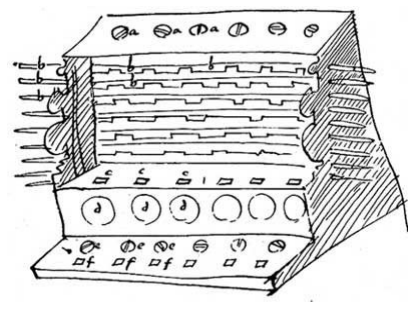
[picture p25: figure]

Es sollte mit dem Speicherwerk (unten in der fertigen Maschine) begonnen werden. Es hat einen mittleren Schwierigkeitsgrad. Wer hier ernste Probleme bekommt, sollte sich lieber gleich Hilfe holen.
Das Multiplizierwerk (für die obere Hälfte der Maschine) ist aufwändiger. Die Konstruktion der Rastfeder des Speicherwerks wiederholen sich hier, Wellen und Montagetricks sind ähnlich. Es hilft, diese vorher schon einmal am weniger kritischen Speicherwerk eingeübt zu haben. Der Schwierigkeitsgrad des Addierwerks ist höher. Hier werden sehr viele Teile mit hoher Präzision zusammengesetzt. Übung macht den Meister.
Schild und Seitenwände sind handwerklich am einfachsten zu bauen. An ihnen kann zwischendurch - zur Erholung oder während Leim trocknet - gebaut werden.

## 3. Speicherwerk (memory unit)

Dieses Werk ist einfacher als die anderen, und sollte zuerst zusammengebaut werden. Das Speicherwerk ist eine flache Kiste (ca. 33 cm lang, 3 cm hoch, 7 cm tief) am unteren Ende der Maschine.
Auf der Oberseite sind sechs Drehknöpfe und sechs Fenster, die je eine Ziffer zeigen. Zu Beginn einer Multiplikation wird hier eine der beiden Zahlen durch die Drehknöpfe eingestellt.
Die Unterseite hat Aussparungen, um einen Blick in den Mechanismus zu erlauben.

6 Einstellräder
1x Welle Mittelteil, 2x Welle Seitenteil, 2x Zahnring, 1x Ziffernscheibe. Die wellige Innenseiten Zahnringe leicht anschleifen und mit Kerzenwachs einreiben. Hier laufen später die Rastrollen.
Auf den Zahnringen ist eine Ziffer “4” angebracht. Diese soll genau unter der großen “4” auf der Ziffernscheibe liegen. Die Ziffernscheibe wird nicht verklebt, nur lose auf die vergrößerte Schulter aufgelegt.

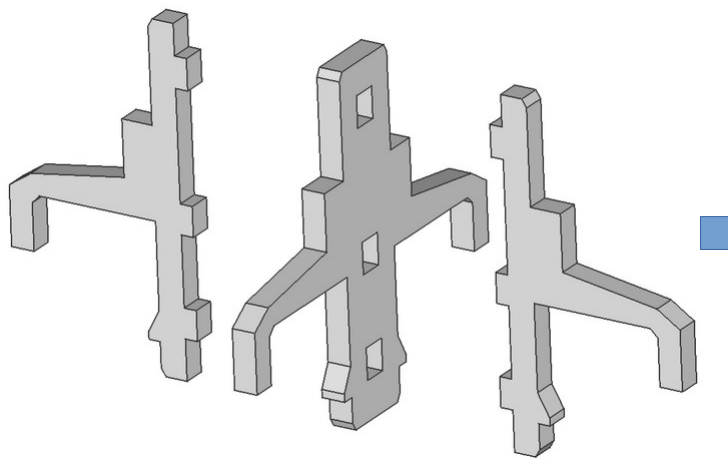
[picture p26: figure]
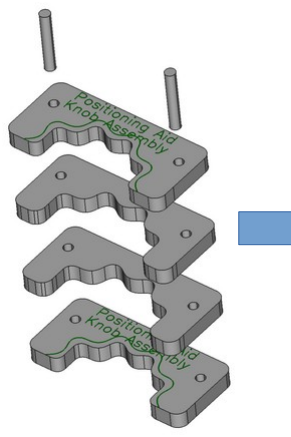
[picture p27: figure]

6 Knöpfe,
bestehend aus je zwei größeren

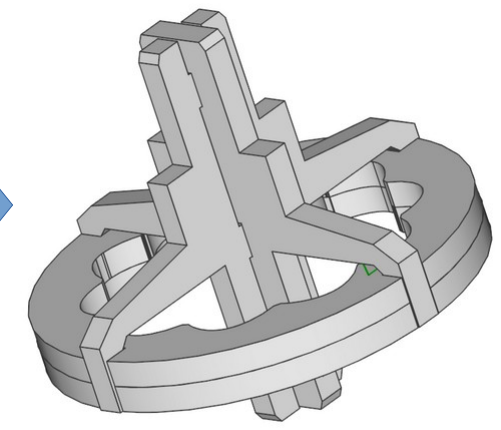
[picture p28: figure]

gezahnten Scheiben (beschriftet mit „3“), einer kleinen Zahnscheibe ohne Loch, einer kleinen Zahnscheibe mit Loch („2“). Weitere 6 Knöpfe werden je für das
Addierwerk und Multiplizierwerk benötigt,
also insgesamt 18 Stück.

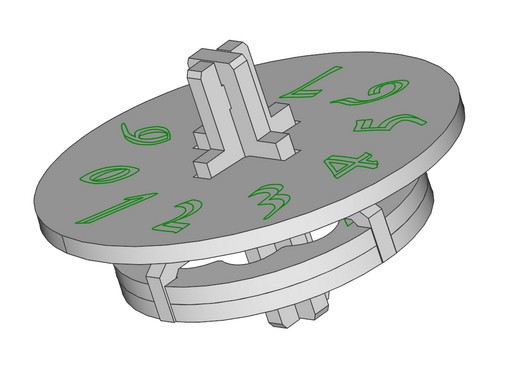
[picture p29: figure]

Zum Verleimen der Knöpfe wird eine Positionierhilfe aus 4 gezackten Plättchen gebaut. Das oberste und unterste Plättchen sind beschriftet. Die vier Zahnscheiben müssen so gestapelt sein, dass sie sich seitlich in die Positionierhilfe schieben lassen, dabei müssen geichzeitig die kreuzförmigen Löcher in drei der Scheiben fluchten.
Das kann mit einer fertigen Wellen geprüft werden. Sparsam leimen. Es sollte kein Kleber ins Innere gelangen!

Plattfeder
6x Achse 4 mm, 12x Ring 8 mm, 6x Ring 11 mm, Federteil groß, Federteil klein. Die „großen“ 11 mm Ringe sollten außen und innen „perfekt“ rund sein. Innen mit einer Rundfeile glätten, außen mit Schleifpapier. Um den Ring zu halten, kann er z.B. auf einer konischen Rundfeile aufgesteckt werden. Nach dem Schleifen mit Kerzenwachs rundherum bestreichen.
Die Federteile nur um die
Langlöcher herum verkleben.

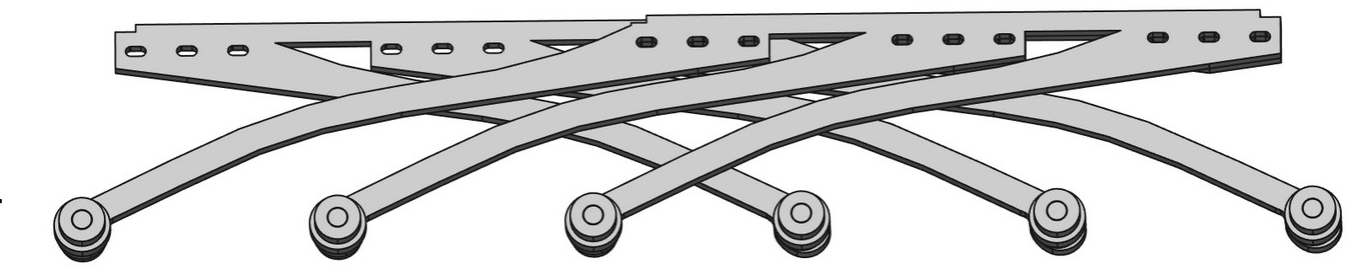
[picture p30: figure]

Die Arme bleiben beweglich. Zur
genauen Positionierung beim
Kleben können je zwei
Zahnstocher durch ein Loch ganz links und ganz rechts durchgesteckt werden. Im obigen Bild sieht man, dass die drei linken Federarme oben liegen, die drei rechten unten. Die großen Ringen sollen alle auf gleicher Höhe zu liegen kommen:
- Bei den drei rechten Armen: Die Achse jeweils so in den Arm kleben, so dass sie unten bündig ist. Ein kleiner Ring wird oben oberhalb des Arms aufgeschoben.
- Bei den drei linken Armen: Die Achse jeweils um 3 mm nach unten aus dem Arm herausstehen lassen. Ein kleiner Ring wird auf diesen unteren Überstand aufgeklebt.
Vor dem Aushärten des Leims prüfen, ob die Achsen rechtwinklig in den Armen stecken. Gegebenenfalls mit einer Spitzzange korrigieren. Herausquellenden Leim vollständig von der Achse entfernen.
Die großen Ringen aufstecken, sie müssen sich sehr leicht drehen lassen. Zum Abschluss wird jeweils noch ein kleiner Ring aufgesteckt, knapp nur soweit, dass der größere Ring sich noch frei drehen lässt. Beim Verkleben dieses letzten Ringes sehr sparsam sein. Es darf kein Leim auf der Unterseite herausquellen.

Gehäuse

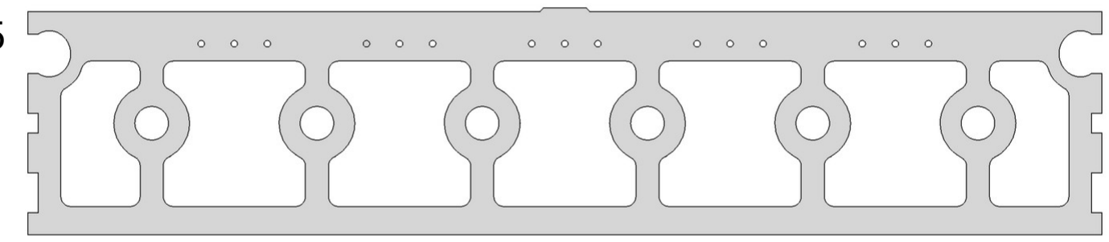
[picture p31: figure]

In die Bodenplatte werden 15 kurze Stücken Zahnstocher
(10 – 15mm lang) eingeleimt.
Diese sollten rechtwinklig
stecken. Gegebenenfalls mit
einer Spitzzange korrigieren, bevor der Leim aushärtet.
Nach dem Aushärten wird die Feder so aufgesteckt, so dass die Zahnstocher mittig in den Langlöchern sind. Sollten später die Zahlen nicht mittig in den Fenstern stehen, kann die Feder noch justiert werden. Dann mit einem kleinen Tropfen Leim auf der Bodenplatte gegen Verrutschen sichern.

Zum Verleimen der Seitenteile und des Gehäuseoberteils Kreppband zum fixieren verwenden. Die langen Seitenteile sind mit dem Oberteil nicht verzapft. Hier muß vor dem Aushärten des Leims gepüft werden daß genau Kante auf Kante sitzt.
Die Bodenplatte wird nicht mit dem Gehäuse verleimt, nur gesteckt.

Die Endmontage mit allen
Wellen und Ziffernscheiben ist
fummelig. Das Gehäuse mit
dem Oberteil nach unten auf den Tisch legen. Die
Wellenstummel werden ca 1.5 cm durch die jetzt unten
liegenden Löcher des Oberteils herausstehen. Dazu das

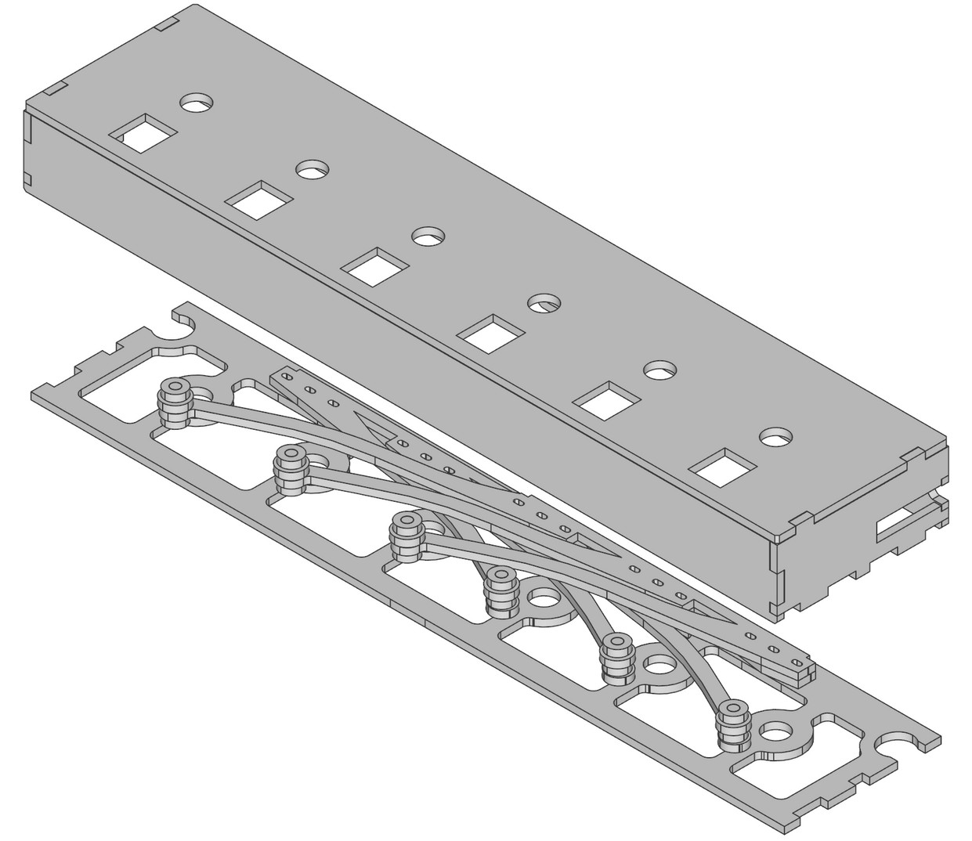
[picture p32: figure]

Gehäuse erhöhen, z.B. auf zwei gleichen Schachteln oder
Büchern.
Nun wird immer eine Welle
zusammen mit ihrer
Ziffernscheibe eingesteckt. Man
beginnt ganz am Rand, Die Ziffernscheiben überlappen sich dabei gleichmäßig. Kontrollieren, dass alle Wellen ganz durch die Ziffernscheiben gesteckt sind.
Die Bodenplatte mit vormontierter Rastfeder wird sich nicht auf Anhieb einsetzen lassen. Es muss bei jeder Welle a) die Rastrolle in die Verzahnung schnappen, b) das Wellenende im Loch des Bodens ankommen. Hierzu beginnt man am besten auch an einer Seite und kann durch Drehen am Wellenstummel die Rastrolle zum Einschnappen bringen.
Etwa ab der Mitte muss auch die hintere Seitenwand ein wenig weggebogen werden, da hier der Zapfen der Bodenplatte in eine entsprechende Tasche einschnappen muss. Sobald alles seinen richtigen Platz hat, sollte die Bodenplatte provisorisch mit Kreppband gesichert werden. (Später wird sie durch die Seitenwände gehalten.)
Die Knöpfe können nun auf die Wellen aufgesteckt werden. Sie sollten nicht verklebt werden, da man sie im Wartungsfall abziehen muss. Jeder Knopf sollte sich mit mäßiger Kraft stecken lassen. Falls er sehr leicht wieder herunterfallen kann, einen kleinen Tropfen Leim seitlich am Wellenende trocken lassen, und zurechtfeilen, um eine entsprechende Verdickung zu schaffen.
Falls sich ein Knopf nicht vollständig aufstecken lässt, die Innenkonturen mit einer kleinen Flachfeile nacharbeiten, oder einen neuen Knopf bauen.

## 4. Multiplikationswerk (napier unit)

Dies ist der obere Teil der Maschine, wo Multiplikationen durchgeführt werden. Benannt nach John Napier welcher die Neper'schen Rechenstäbe erfand. Siehe auch https://en.wikipedia.org/wiki/John_Napier
Dieser Teil sollte nach dem Speicherwerk gebaut werden.
Das Multiplikationswerk ist eine Kiste (ca. 33 cm x 21 cm x 6 cm) mit 6 aufrecht stehenden Walzen. Die Rückseite ist offen, um Anordnung der Walzen zu zeigen. Die Vorderseite wird von 8 Schiebern verdeckt, die in den Schlitzen der Seitenwände stecken und nicht mit dem Multiplikationswerk verbunden sind. Die Schieber können jeweils eine Zeile in der Multiplikationstabelle abdecken oder freigeben. An einer Seite wird eine Zickzack-Plattfeder mit 8 Federarmen eingeklebt, so dass die Köpfchen der Feder jeweils 1 mm aus der Front herausragen. Diese Köpfchen bremsen die Schieber.
Im Deckel wird noch einmal die gleiche Federkonstruktion eingebaut wie im Speicherwerk. Hier sind allerdings die Löcher für die Zahnstocher nicht gebohrt, da diese sonst oben sichtbar wären. Die Federteile sollten nur punktuell in den Deckel eingeklebt werden. Eventuell ist eine Nachjustage nötig, damit die Ziffern mittig in den Fensterchen stehen. Der Deckel wird nicht mit dem Rest der Einheit verklebt. Die Knöpfe werden erst nach Einbau in den Seitenwänden aufgesteckt, nicht verklebt.

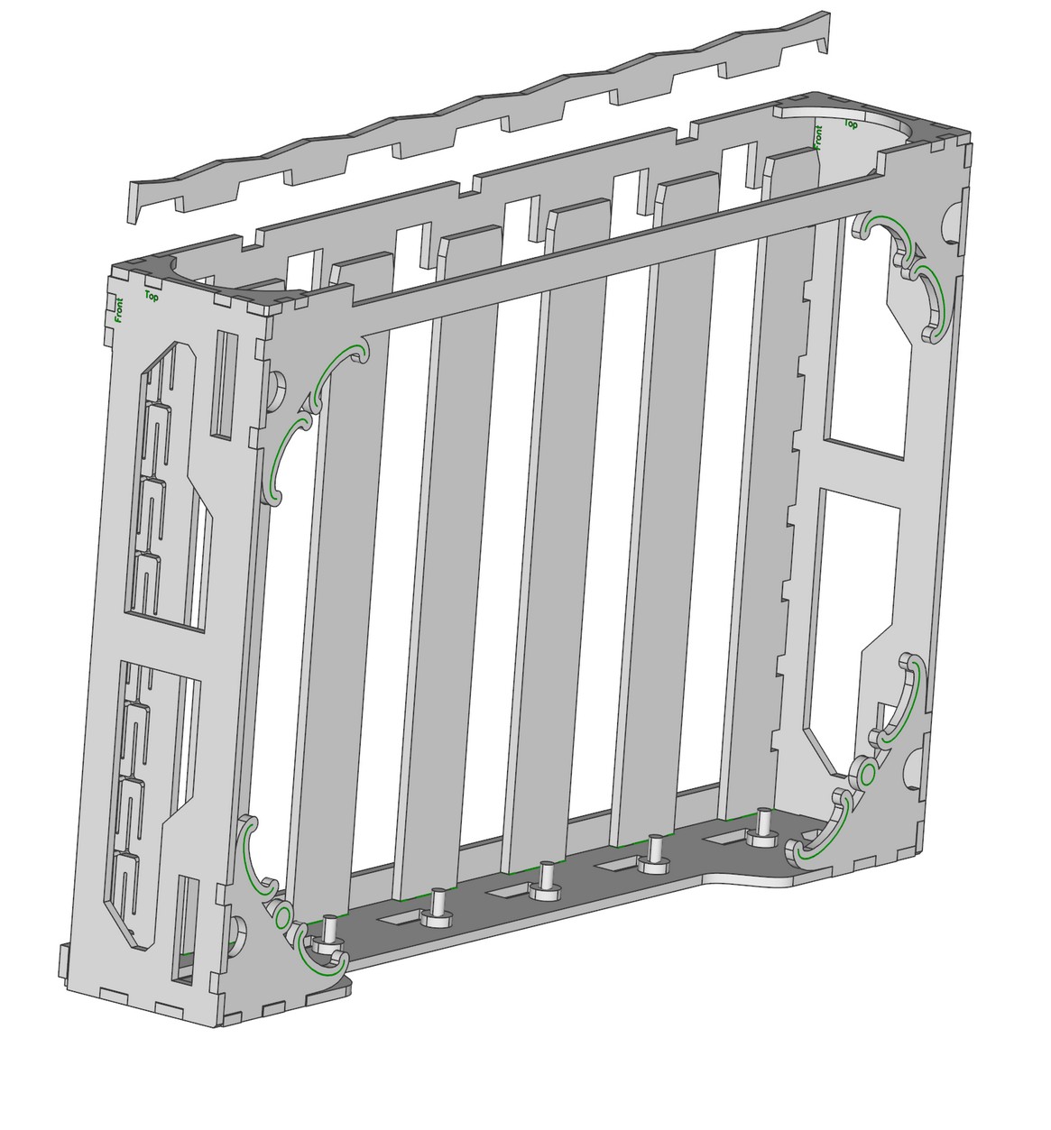
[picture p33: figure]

Abbildungen:

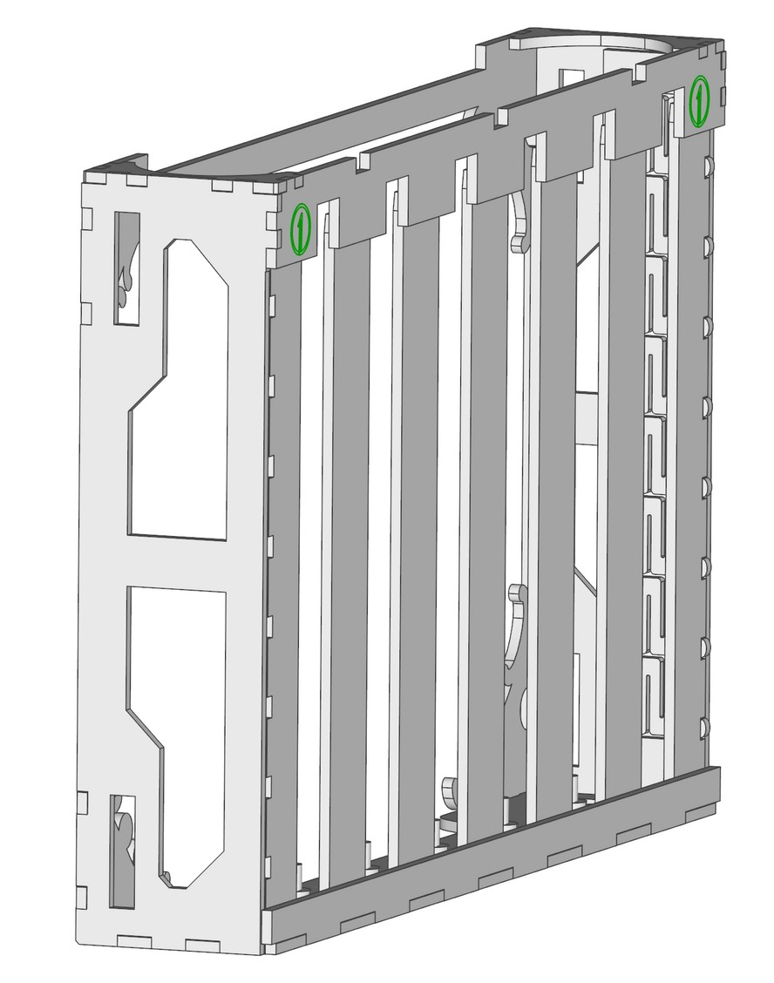
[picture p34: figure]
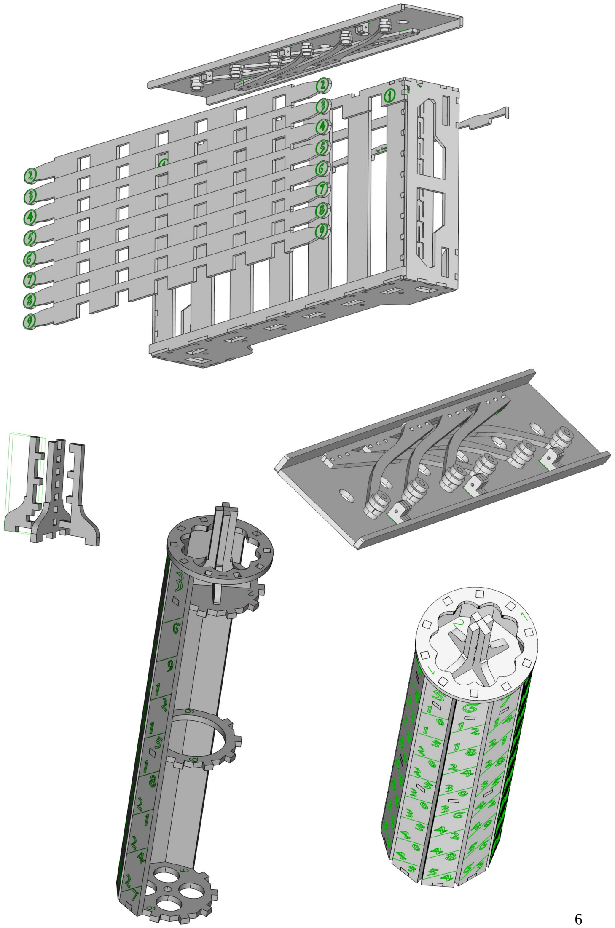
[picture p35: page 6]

## 5. Addierwerk (adder unit)

Das Addierwerk ist ein Kiste (ca. 33 cm x 8 cm x 8 cm) in der Mitte der Maschine. Auf der Vorderseite sind sechs Knöpfe mit Scheiben mit je 10 Löchern. Das Addierwerk kann mit einem 6mm Rundstab oder einem Stift bedient werden, welcher in die Löcher einsticht. Die Oberseite der Kiste hat sechs Fenster, die das Rechenergebnis anzeigen.
Die Kiste hat keinen Boden und die Rückwand ist durchbrochen, so dass der komplizierteste Teil der Maschine gut sichtbar ist: Das Räderwerk. Dieser Mechanismus dient dem Zehnerübertrag zur jeweils nächsten Stelle. Wilhelm Schickard war vermutlich der erste, der einen solchen Mechanismus erdacht und gebaut hat. Siehe https://en.wikipedia.org/ (https://en.wikipedia.org/wiki/Wilhelm_Schickard) wiki (https://en.wikipedia.org/wiki/Wilhelm_Schickard) /Wilhelm_Schickard. (https://en.wikipedia.org/wiki/Wilhelm_Schickard)

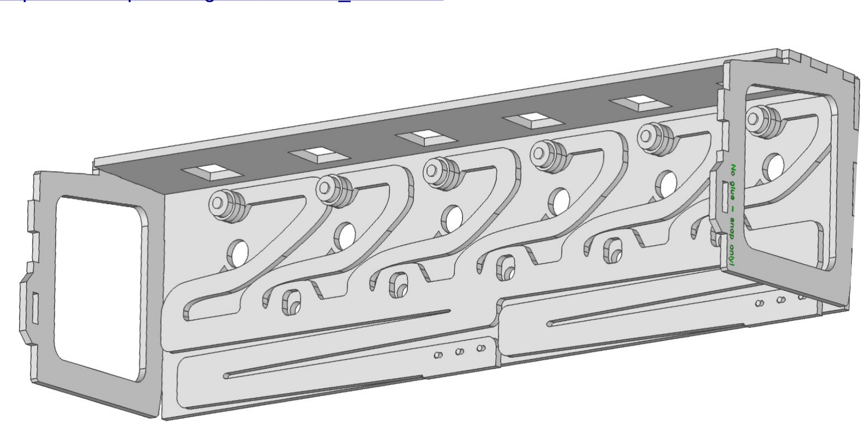
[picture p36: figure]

Die Frontplatte der Kiste hat am unteren Rand zwei Dreiergruppen Bohrungen für Stifte mit 2mm Durchmesser. Diese Stifte werden aus Zahnstochern geschnitten, je ca. 10-15 mm lang. Sie werden so in die Frontplatte eingeklebt, dass sie auf der Innenseite herausstehen. Nach dem Aushärten werden eventuelle Überstände außen verschliffen. Die Stifte halten später die Rastfeder.
Die Rastung der Räder wird durch eine komplexe Feder erreicht. Im Gegensatz zu den Federn im Speicherwerk und im Deckel des Multiplizierwerks besteht diese Feder aus einer Federplatte, die nach oben hin sechs kürzere, und nach unten hin 2 längere Federarme hat. Alle Arme dieser Federplatte müssen frei von Schäden sein, und mit Fingerkraft ca. 1mm nachgeben ohne zu brechen.

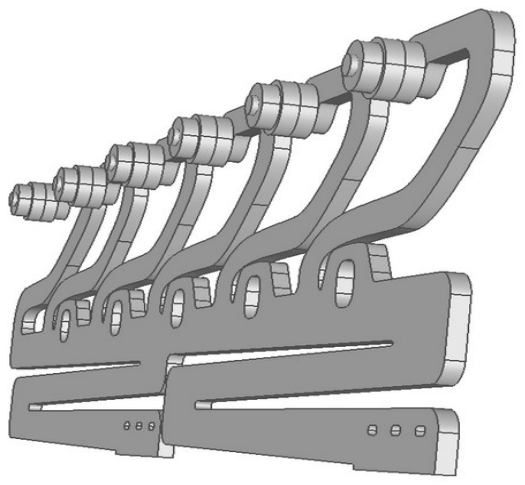
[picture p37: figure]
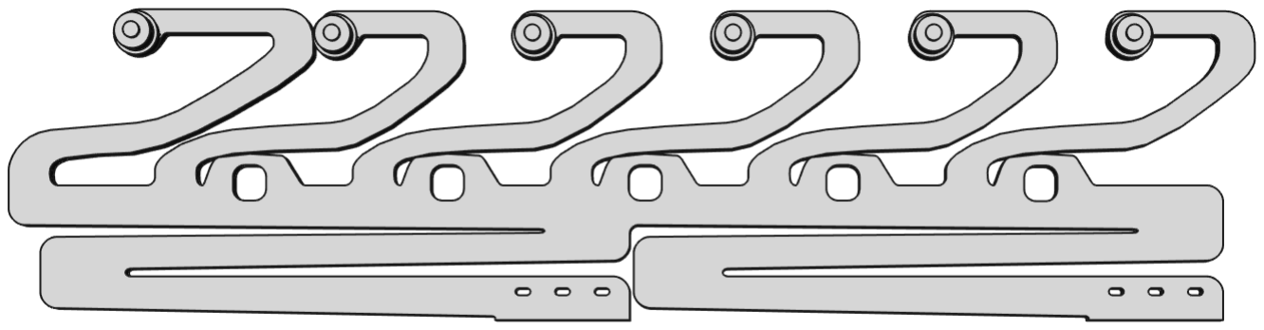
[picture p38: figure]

In die Augen der sechs kurzen Federarme werden 4mm-Achsen eingeklebt. Auf jede Achse werden zwei 11mm Ringe lose aufgesteckt, und mit einem verklebten 8mm Ring gesichert. Die 11mm Ringe müssen ohne Reib- oder Quietsch-Geräusche leichtgängig laufen. Mit reichlich Kerzenwachs schmieren. Die fertige Feder wird mit ihren 6 Langlöchern auf die Stifte gesteckt, aber nicht verklebt. Durch Verschieben in den Langlöchern wird das Addierwerk später justiert.

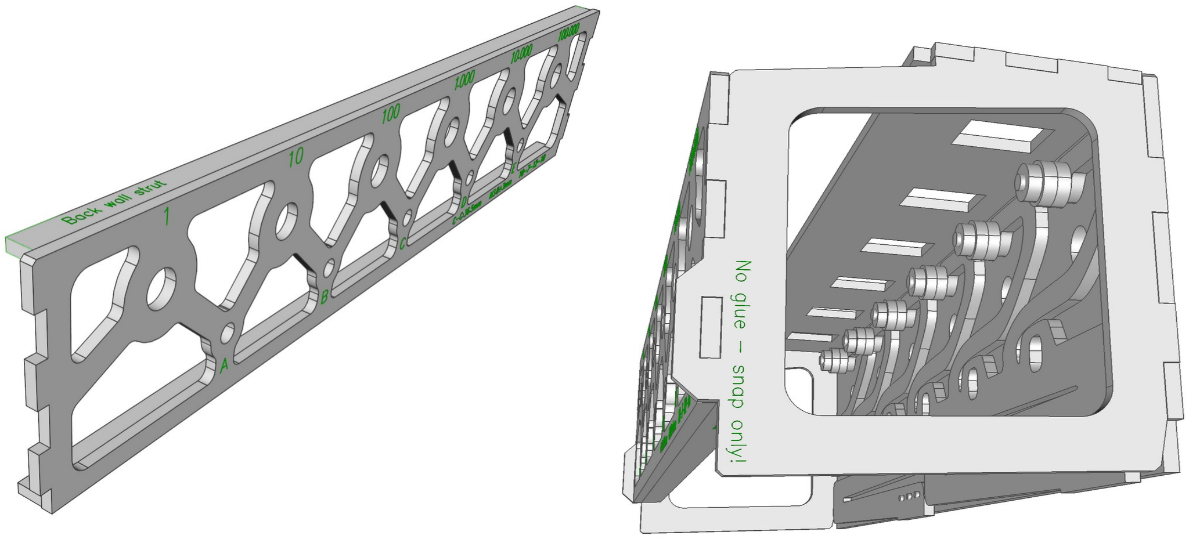
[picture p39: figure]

Die Rückwand besteht aus einer stark durchbrochenen Platte mit sechs großen Rundlöchern oben (beschriftet mit 1, 10, 100, 1.000, 10.000, 100.000) und 5 kleineren Rundlöchern unten (beschriftet mit A, B, C, D, E). An der oberen und unteren Kante der Rückwand werden je eine Stabilisierungsleiste (beschriftet mit “back wall strut”) nach innen zeigend aufgeklebt. Die Rückwand wird (nach Einbau aller Räder) in die Seitenteile eingerastet. Nicht verklebt.
Die sechs Haupträder bestehen je aus einem Kopf mit Scheibe, einer Ziffernwalze, einer Kreuzwelle und diversen Zahnrädern. Knopf und Ziffernwalze sind immer gleich, aber Welle und Zahnräder müssen in zwei Varianten (zu je drei Stück) gebaut werden. Lochscheibe und Knopf müssen so verklebt werden, dass immer die “schöne Seite” der Lochscheiben zum Knopf zeigt. Als Montagehilfe dafür können beide Teile auf eine Welle (siehe unten) aufgesteckt werden, die Welle ist zu ziehen bevor der Kleber aushärtet, da später die Wellen von innen und die Knöpfe von außen montiert werden müssen. Die Position der '0' ist mit einer kleinen Kerbe auf der Lochscheibe markiert. Diese Markierung muss bei der Endmontage beachtet werden.
Die Ziffernwalze wird aus einem Ring mit welliger Innenverzahnung, einer Scheibe und 10 Ziffernplättchen aufgebaut. Auf Ring und Scheibe ist die Position der '0' jeweils durch ein Rechteck markiert. Die ‘1’ liegt links neben der ‘0’, die ‘9’ rechts.
Die Wellen bestehen aus drei Teilen, die kreuzförmig verklebt werden. Es gibt zwei verschiedene Sätze Wellenteile, beschriftet "1, 100, 10.000" bzw. "10, 1.000, 100.000". Auf jedes Wellenkreuz wird zuerst eine fertige Ziffernwalze geklebt. Die Ziffernwalze wird von hinten aber mit der offenen Seite voran auf die Welle geschoben, so dass die

Bodenscheibe der Ziffernwalze schließlich genau winklig auf 4 kleinen Zapfen sitzt und dort verklebt werden kann.

Zahnräder und Abstandsquadrate werden ebenfalls von hinten auf die Wellen gesteckt. Die Schrift zeigt bei allen Aufsteckteilen immer nach hinten. Alle Aufsteckteile haben je zwei Zahnstocherbohrungen. Diese müssen fluchten. Die großen 10-Zähne-Räder haben die Position der '0' mit einem Strich markiert.
Die Reihenfolge, in der die Teile auf die Wellen gesteckt werden, ist wie folgt:
3 Wellen "1, 100, 10.000":
- erst 2x Einzahn,
- dann 4x Abstandsquadrat,
- dann 2x 10-Zähne-Rad.
3 Wellen "10, 1.000, 100.000":
- erst 2x 10-Zähne-Rad,
- dann 4x Abstandsquadrat,
- dann 2x Einzahn.
Dabei sind die beiden Zahnstocherlöcher immer links. Mit den Zahnstochern werden alle Teile genau ausgerichtet. Alle bis auf das letzte Teil werden ohne Leim aufgesteckt, nur das letzte Teil und die beiden Zahnstocher werden verklebt. Überstehende Spitzen der Zahnstocher können abgeschnitten werden.

Die fünf Zwischenräder (carry wheels) bestehen aus je einer runden Welle, einer Gruppe Zahnrädern, und je zwei kleinen Ringen.
Die Wellen sind 6mm Buchenrundstäben, 90mm lang. Die Ringe haben 12mm Durchmesser.
Auf der Rückwand sind die Positionen der Zwischenräder A, B, C, D, E beschriftet. Für die genaue Position der Zahnradgruppe gibt es zwei unterschiedliche Montagehilfe (Positioning Aid Carry Wheels). Mit der Montagehilfe “A,C,E” werden drei Stück aufgebaut, mit der Montagehilfe “B,D” nur zwei.
Die Montagehilfen entsprechen der Draufsicht von oben. Sie haben passende Öffnungen für die Ringe und Räder. Auch hier werden zwei Zahnstocher zur genauen Ausrichtung eingeklebt. Nur ein Ring wird entsprechend der Montagehilfe an der Innenseite der Rückwand auf die Welle geklebt. Der zweite Ring wird später von außen auf die Welle gesteckt, um die Welle in der Rückwand zu Positionieren. Sitzt dieser Ring locker, kann er leicht geklebt werden. Er sollte im Wartungsfall gelöst werden.

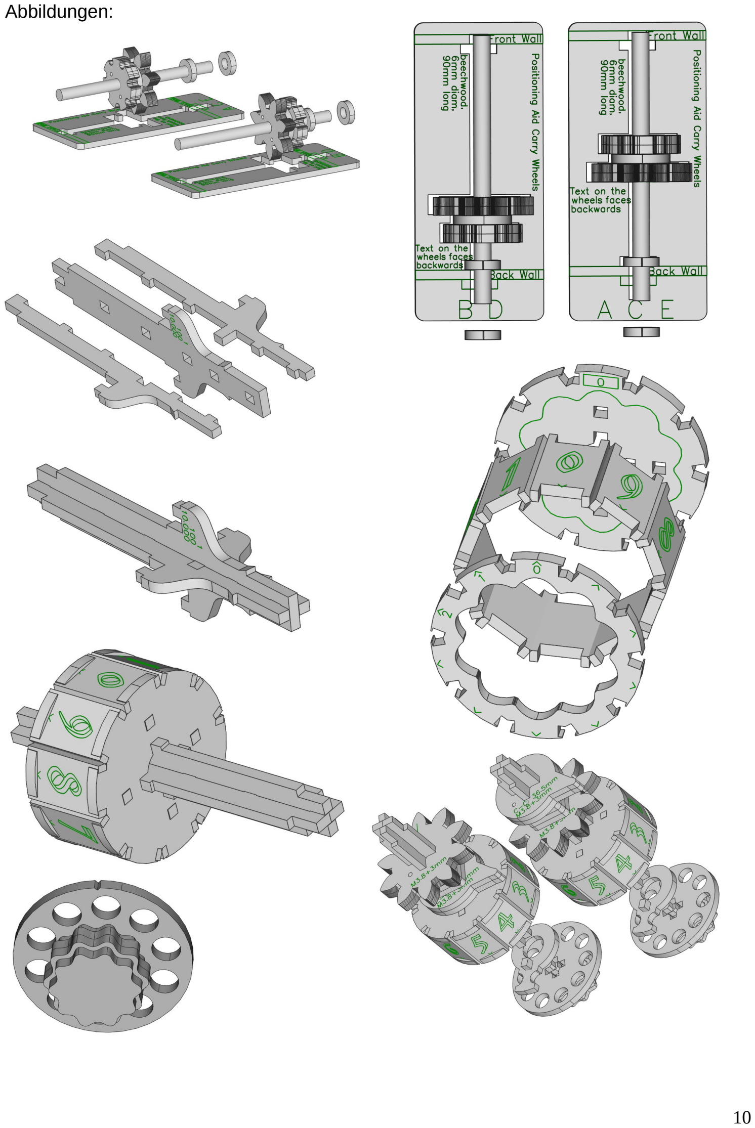
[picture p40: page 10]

Abbildungen:

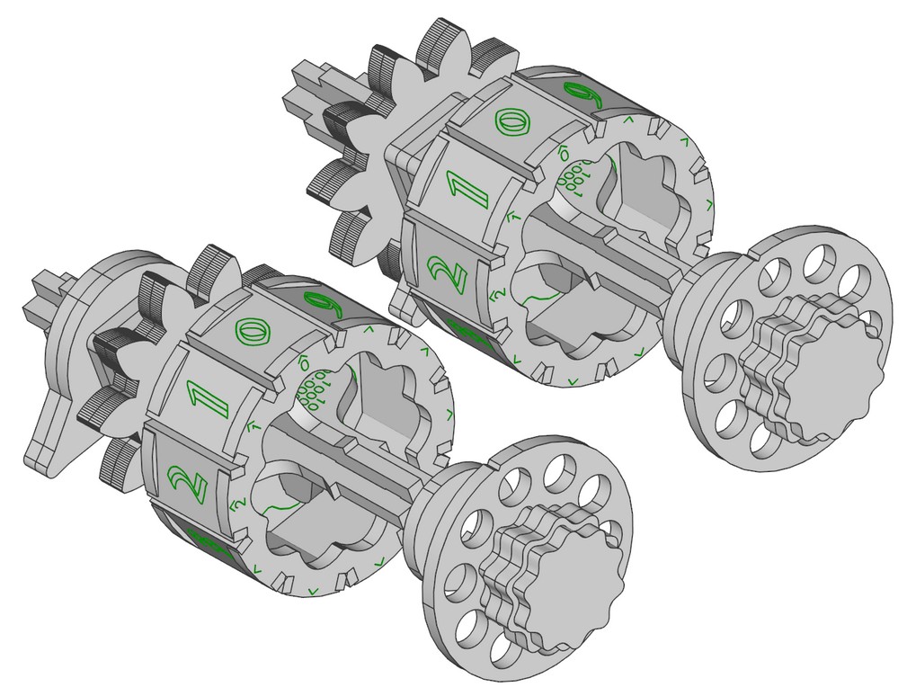
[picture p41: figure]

## 6. Seitenwände

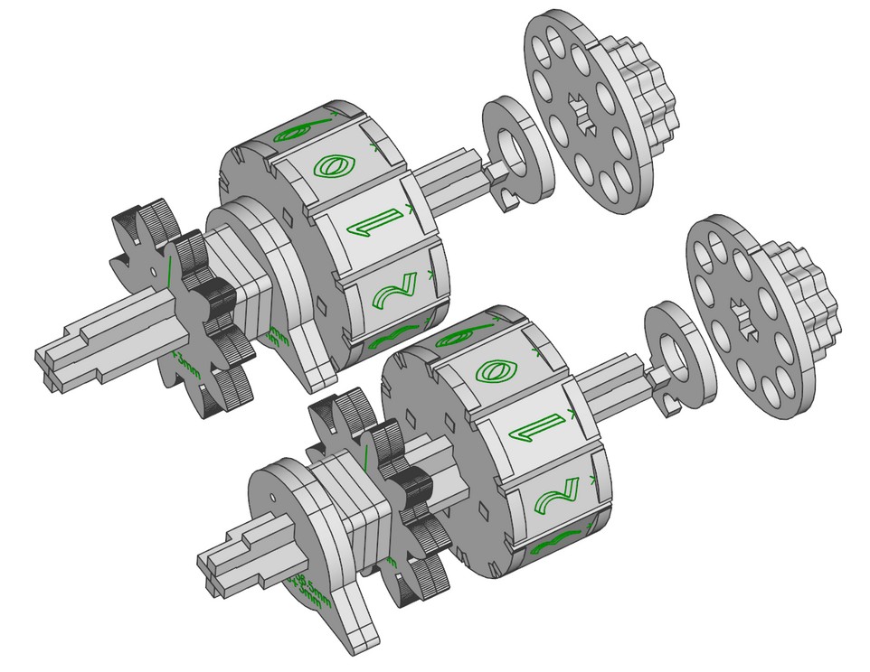
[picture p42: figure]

Die Maschine ist modular aufgebaut. Jedes der drei Werke hat ein eigenes Gehäuse. Die linke und rechte Wand der Maschine halten die drei Werke in Position. Jede Wand besteht aus zwei Lagen Holz. Die innere Lage hat Aussparungen passend für die drei Werke. Zum Verleimen die beiden Lagen mit vielen Wäscheklammern exakt(!) fixieren. Bevor der Leim aushärtet, sollte kontrolliert werden, dass kein überschüssiger Leim in den Aussparungen für die drei Werke gelaufen ist.
Das Speicherwerk wird später mit zwei Verbindern und zwei Keilen in den Wänden gehalten. Das Multiplizierwerk hat vier Verbinder und Keile, das Addierwerk keine.
Ein Wandverbinder besteht aus zwei gleichen Teilen. Diese werden mit Zahnstochern verstiftet und verleimt. Die lange gerade Grundfläche sollte geschliffen werden, damit die spätere Klebung auf der Seitenwand sehr gut hält. Für die genaue Positionierung aller Wandverbinder gibt es Positionierhilfen. Sollte bei einer Steckprobe ein Werk klemmen, dürfen die Öffnungen entsprechend ausgefeilt werden.
In jede Seitenwand werden außerdem drei kleine Brettchen eingeleimt, die duch eine verzierte Halteleiste verbunden sind.

Montage
Als erstes wird eine Seitenwand auf den Tisch gelegt, und das Multiplizierwerk aufgesetzt. Zum Hantieren des Multiplizierwerkes sollte der Deckel mit Kreppband gesichert werden. Sobald das Multplizierwerk samt Deckel flach in der Aussparung sitzt wird es mit zwei Keilen befestigt.
Es sind drei verschiedene Stärken Keile im Bausatz, insgesamt werden nur 6 Keile verwendet. Falls ein Keil ganz im Loch verschwindet, einen dickeren verwenden.

Multiplizierwerk mit Seitenwand werden nun (etwas wackelig) auf den Rücken gelegt. In dieser Position können die 8 Schieber vor dem Multiplizierwerk durch die Seitenwand gesteckt werden.
Die zweite Seitenwand wird zuerst auf alle 8 Schieber-Enden aufgefädelt, und dann das Multiplizierwerk in die Aussparung eingerastet. Zum Verkeilen kann die Maschine vorsichtig aufgestellt werden, ohne dass etwas auseinander fällt.
Ist das Multiplizierwerk mit allen vier Keilen fest mit den Seitenwänden verbunden, kann die Funktion der Schieber kontrolliert werden. Sie sollten sich mit leichter Handkraft bewegen lassen, aber nicht lose verrutschen, wenn andere Schieber bewegt werden, oder die Maschine geschüttelt wird. Sind die Schieber zu lose, kann eine zweite Federplatte auf der anderen Seite ins Multiplizierwerk geklebt werden. Sind die Schieber schwergängig, sollten die Seitenwände noch einmal abgenommen werden, um die 8 Köpchen der Federplatte abzufeilen. Eventuell auch die Durchbrüche in den Seitenwänden ausfeilen, und die Kanten der Schieber mit Schleifpapier glätten.

Ebenso sollten sich alle 6 Walzen leicht drehen lassen. Die Walzen sollten in allen Positionen gleichmäßig rasten, so dass die Ziffern in den Fenstern gut lesbar sind. Sie müssen nicht genau mittig sein, aber falls sie zu weit an den Rändern der Fenster einrasten, sollte das Multiplizierwerk noch einmal demontiert werden, um die Rastfeder im Deckel zu versetzen. Die Klebung kann mit einem scharfen Werkzeug Schraubenzieher, Spachtel, Messer noch gelöst werden, wenn sie noch nicht zu alt ist.
Wenn das Multiplizierwerk und die Schieber einwandfrei funktionieren, kann das Addierwerk von vorne zwischen die Seitenwände geschoben werden. Es schnappt in beiden Wänden in die entsprechenden Aussparungen.
Schließlich wird das Speicherwerk ebenfalls von vorne zwischen die Wände geschoben. Dabei müssen sich die Wände etwas weiter aufbiegen, da hier die Wandverbinder in die Seiten des Werkes schnappen müssen.

Liegen beide Werke flach in ihren Aussparungen, kann die Maschine vorsichtig auf den Rücken gedreht werden, so dass die letzten beiden Keile von unten ins Speicherwerk eingesetzt werden können.

Damit ist der Aufbau komplett!

Die kleinen Brettchen auf der Rückseite der Maschine dienen der Aufbewarung von Schild und Bedienstiften. Stifte kann man an beiden Seiten jeweils durch die Löcher der oberen beiden Brettchen stecken. Das Schild kann man überkopf mittig zwischen die hervorstehende Ecken der Brettchen einstecken.

Abbildung:

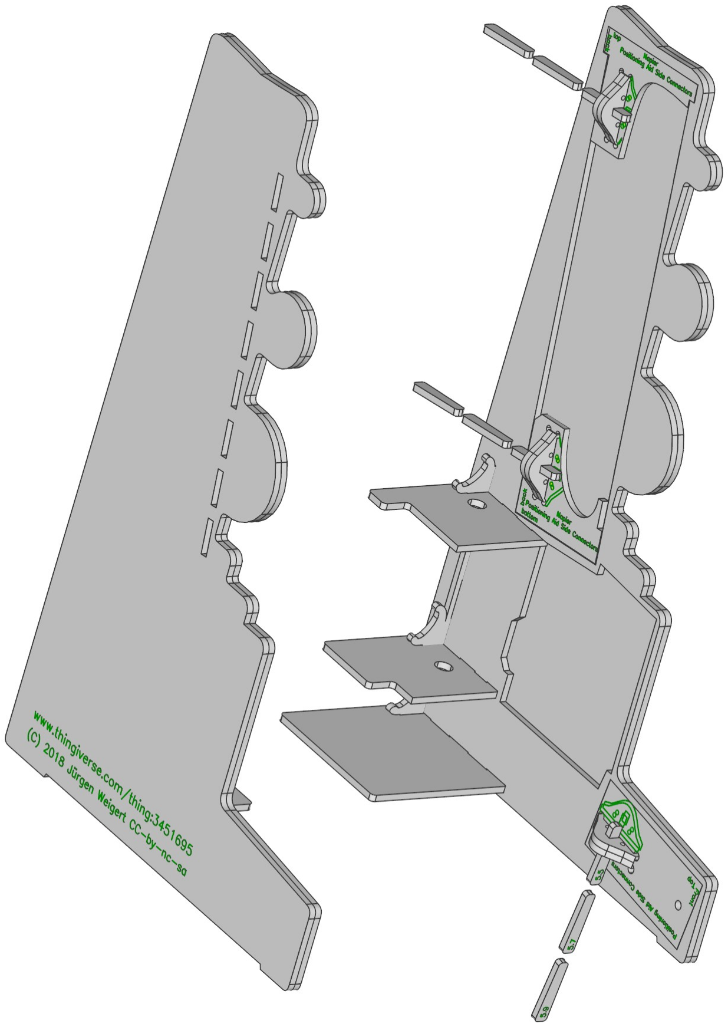
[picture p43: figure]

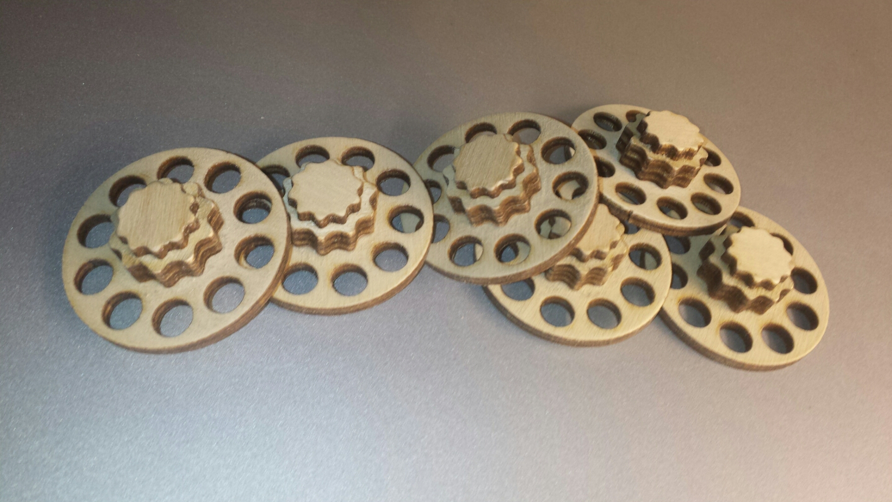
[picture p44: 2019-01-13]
photos/build/20181030_131505.png

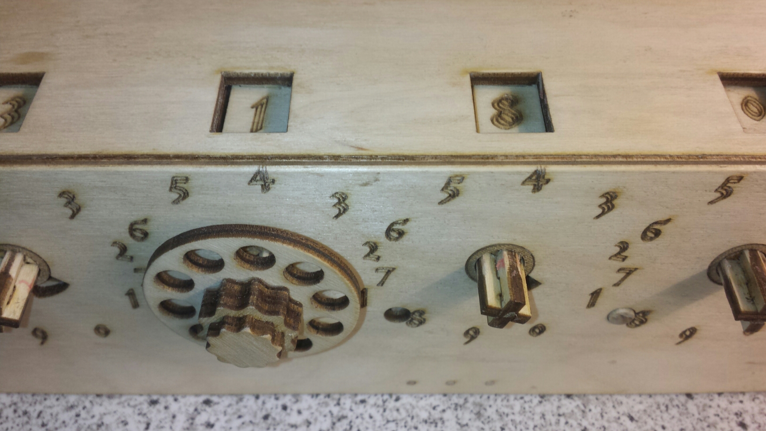
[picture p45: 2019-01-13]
photos/build/20181030_131336.png

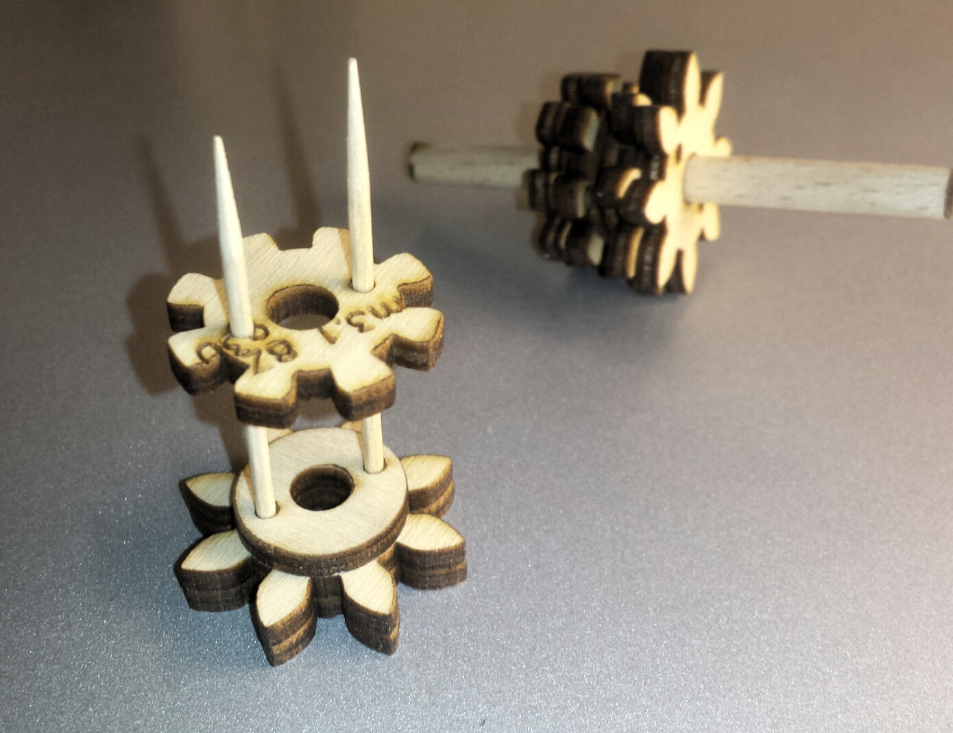
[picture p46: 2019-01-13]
photos/build/20181030_131315.png

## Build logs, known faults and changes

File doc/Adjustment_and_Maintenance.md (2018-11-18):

Grease before assembly
======================
All moving parts should be rubbed with wax. The stump of an old candle works fine for that
purpose. Especially take the time to

1) apply wax to all faces of the the small rollers at the tips of the springs.
2) apply wax to all teeth of each gear.

Apply very little wax to the sliders. It okay for them to 
have some friction, as there are no springs to hold them in position.

After assembly, if you find that some knobs turn harder than others or make unusual noise, 
you may re-apply some wax. It may be needed to open the neper drum box and the memory unit to access
the interior, for the adder unit, the tip of a small knive (carrying some wax) should help to reach all parts.
There should be no grinding or creaking noise from the machine. Only the clicking of the springs
when a digit snaps into position.

Adjustment of the adder unit after assembly
===========================================

There is one long tooth per wheel that engages in its left
neighbour to perform a carry over.
This happens, when the wheel is turned clockwise from 9 to 0 (addition) 
and also when turning counter clockwise from 0 to 9 (subtraction).
This tooth engages only in betwwen the 0 and 9 positions.
It must not be engaged when the wheel sits in the 0 or 9 position.
The wheel left to it must rotate freely in both cases.

To achieve this setting, the wooden spring at the back of the adder unit can be moved 
sideways by 2mm.

1) Start by moving the spring centered, so that there 1 mm travel to either side.
2) Turn the wheels of the adder unit until it displays 9 9 9 9 9 9.
3) flip the machine over and find the one long tooth on each wheel of the adder unit.
4) Looking at the back of the adder unit, each long tooth should point south-east
   and should be ca 0.5mm away from the neighbouring gear. 
   The gap can be seen best when looking into the adder unit from the bottom.
   Cut small strip from a business card, it should easily slide between tooth and gear.
5) If they are too far away, push the spring a fraction of a millimeter leftwards. The gap gets smaller.
6) If they touch or engage the gear, push the sping rightward until they don't.
7) Turn the wheels of the adder unit until it displays 0 0 0 0 0 0.
   If perfectly turned, turing the rightmost (unit) wheel clockwise should turn all wheels.
   Initially, it may be very hard to do so. Turn the unit wheel rightward, until you see the
   thenths, hundreds, and thousands wheel move just a tiny bit. To complete the movement at the unit wheel, 
   help with your other hands gently at the thousands wheel.
   If that works, the unit is tuned 'good enough'.
   If the mechanism blocks, turn each wheel individually counter-clockwise all the way from 9 to 0.
8) flip the machine over again and find the one long tooth on each wheel. It is now a bit higher into the
   mechanism pointing east-shouth-east.
9) Again, each long tooth should not be engaged. It should be away from the gear the same amount 
   as it was on the first place.
10) If needed, adjust the spring, then apply some glue near the pins to lock the spring in the 
   best position.
11) In case there is no spring position for all long teeth to be free simultaneously in both (0 and 9) positions, 
   gently apply a small file to remove material from the long teeth.

All wheels should now rotate freely, regardless of their neighbours position.
During addition the wheels should never block. It may occasionally happen during subtraction, 
that a wheel blocks when its right neighbour shows 0. Unblock the wheel by holding back its 
right neighbor by a small amount. If that happens too often, check the alignment of the spring, 
and re-adjust according the above procedure.  The wooden construction is sensitive to changes in 
temperature and humitdity, or may simply develop more slack over time.

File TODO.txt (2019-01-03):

[x] * Make number 6 and 5 more distinguishable

[x] * Split up into 3 more files: neper.svg, adder.svg, memory.svg

[X] * Seitenwände und Schild in den memory und neper platten unterbringen

[x] * Seitenwände am Stück, mit neuen Aussparungen für Addierwerk und neuen Ankern für Speicherwerk.

[x] * Halterung hinten für Schublade, Schild, Stift

[x] * Neuer Deckel für Multiplizierwerk. Lagerung der Walzen mit Verstärkungsringen.

[X] * Multiplizierwerk um 2mm pro Zeile gestreckt, damit man es besser ablesen kann. 

[X] * Gehäuse auf beiden Seiten je 6mm breiter

[X] * Multiplizierwerk: Frontblende durch Stützleisten hinter den Schiebern ersetzen.

[X] * Addiergehäuse für 4 Ebenen

[X] * Addiergetriebe mit kleinerer übersetzung, mehr Toleranz

* Rastfeder für Addierer: Mehr individuelle Wege, mehr Vorspannung.

* Tonzunge und Hammer für 1.000.000 Überlauf ?

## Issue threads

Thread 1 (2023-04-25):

Ober- und Unterteil gegeneinander verschiebbar machen

RokerHRO, 2023-04-25:
Beim Multiplizieren muss man sich im Kopf merken, welche Stelle man gerade multipliziert und dann die von den Walzen abgelesene 2stellige Zahl schräg versetzt an der richtigen Stelle aufaddieren.

Die 6 senkrechten Walzen (und die Schieber zum Abdecken/Öffnen der jeweiligen Zahl im Einmaleins) haben ja keine mechanische Verbindung zu den Zahnrädern im Addierwerk.

Könnte man das Oberteil mit den 6 Walzen (und ihren Schiebern) gegenüber dem Addierwerk verschieben, wäre das Rechnen einfacher und weniger fehleranfällig, da man dann nur noch gerade nach unten gehen müsste um das passende Zahlenrad weiterzudrehen.

Klar, das wäre dann nicht mehr ein Nachbaru von Schickards Rechenmaschine, sondern eine verbesserte "Nachfolgeversion", mit verbesserter Bedienung, ohne jedoch am grundsätzlichen Funktionsprinzip etwas zu ändern.

Sind solche "Updates" gewünscht?

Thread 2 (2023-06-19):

3.2mm vs 3mm Platten

fyr77, 2023-06-19:
Hallo!
In den Anleitungen wird generell von 3.2mm Platten gesprochen, der Link zu Ebay (welcher nicht mehr funktioniert) scheint allerdings auf 3mm Platten zu verlinken.

3mm sind um einiges leichter zu finden als 3.2mm. Ist es möglich, das Projekt mit 3mm Platten zu bauen?

Danke!

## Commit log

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2018-10-25 15 extra buttons added to fill laser neper box
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2018-10-26 laser layers for neper box and adder done.
2018-10-27 found the new spring on a test layer.. moved to laser adder.
2018-10-27 cloneed dashes on laser neper drum resolved.
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2018-11-13 new design of the adder gear. May or may not work. The 10 + 7 collide. We need more layers, if at all possible.
2018-11-22 pointed mono-tooth with a 3mm tip. looks promising.
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2018-12-11 missing wheels now in read. baeeh.
2018-12-17 0.1mm laser kerf adjustments and +/-1° tolerances.
2019-01-02 Neuer Deckel für Multiplizierwerk. Lagerung der Walzen mit Verstärkungsringen. Multiplizierwerk um 2mm pro Zeile gestreckt, damit man es besser ablesen kann.
2019-01-02 Gehäuse auf beiden Seiten je 6mm breiter Multiplizierwerk: Frontblende durch Stützleisten hinter den Schiebern ersetzen. Addiergehäuse für 4 Ebenen
2019-01-03 integrated 12-7-10-3mm.svg as a construction layer into schickard_adder.svg
2019-01-04 Adder spring completed, layout squeezed into 3 full board 76x50cm.
2019-01-04 bugfix adder spring. Started Knob Assembly Aid.
2019-01-04 added two missing neper drumms to the layout in 3 boards. Moved the sign to schickard_sign.svg, it is designed for 4mm plywood.
2019-01-07 rearranged folders. Renamed neper to napier for consistency. Copied the knob assembly aids from adder to memory so that memory can be assembled first. Completed Parts_and_Lasersettings.md WIP german 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
2019-01-18 inner parts of the sidewalls stabilized with a 10x3.2mm bridge. cut outs for these bridges made in the adder front. 25mm knobs marked with '3', 22mm knobs marked with '2' (both had '3.2')
2019-02-19 squeezed out 2mm margin of all three schickard_adder.svg schickard_memory.svg schickard_napier.svg boards.
2019-02-21 adder spring more stable and stiffer in the bottom. Added missing back wall to mem
2019-02-25 Flipped side wall in schickard_memory.svg so that we never have laser dirt on a ny outside face. Added thingiverse URL.
2019-03-09 mirrored the ornamented connector on the back side, so that we have a left and a right one with outwards facing ornament.
2019-03-09 Mirrored the ornamented connector on the back side, so that we have a left and a right one with outwards facing ornament. Moved the zigzag of the middle back side shelves so that they cannot be confu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
2019-03-09 X 3 x 3knob verdreht. X knob: Viele innenkreuze sind nicht ausgerundet. X bodenplatte nubsi nach hinten X memory: 10er ring braucht eine '4' Markierung! X memory: bohrlöcher oben 0.1mm grösser, unten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
2019-04-08 flipping back shelf to actually have mirror imaged parts. thighter packing in memory board.
2019-04-08 moved holes in shelves for better access, enlarged bottom shelf, so that booklet cannot fall through.
2019-04-12 Adder: numeral pads width minus 0.2mm to save the work of grinding inner corners.
2019-04-12 Translated adder unit description from en to de.
2019-04-13 all adder shafts were wrong type. Fixed. Now I have some empty space in the board :-)
2019-04-13 adder: zero position of 10 tooth gear marked.
2019-04-13 Adder: Need 24 spacers (not 6). Changed 30mm diameter spacers into 18mm square spacers to fit them all. Documented the mounting sequence for the 6 shafts.
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2019-04-13 adder: bugfix shaft composition.
2019-04-14 Web cam tool to present the machine with maximum resolution. Allows the camera to come from any angle and projector to have resolution than camera.
2019-04-15 adder: only glue the last part per shaft.
2019-04-16 adder: added 12 sturdy 12x5.8 mm washers. Made the inner gaps in the carry positioning aids smaller to allow some tolerance
2019-04-16 adder: no more rings in the walls. memory: numeral disk 2mm more diameter
2019-04-19 memory box 1mm higher. Springs cannot move freely as it was.
2019-04-19 adder: top wall sloped 3° to make 2mm more room for the mono-tooth ... Labeled the two back wall struts, made them 7mm instead of 5mm.
2019-04-19 napier: add holes in bottom of box for mono-tooth of adder. It needs 1mm, we give 2mm.
2019-04-22 adder: extra springs for experiments. adder: changed all 2.0 mm holes to 1.8mm -- toothpicks fit was way to loose.
2019-04-22 adder: spring 0.5mm extra tension at unit position (instead of 1.0mm that was definitly too much)
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2019-04-22 memory: box rear box wall got two notches rounded, where no glue should be applied. more napiers drum shafts turned horizontal.
2019-04-22 memory+napier: made slots for wall connectors 0.8mm wider. napier: moved wall connectors 2mm inwards.
2019-04-22 all corners of the three boxes camfered 1mm to make room for excessive glue in the openings of the side walls.
2019-04-23 napier: added 1mm camfer to the sides of the lid, made the lid 0.2mm wider.
2019-04-23 moved napier and memory spring lower 3 pins by 0.5mm inwards. adder box: slots for wall connectors 1mm longer.
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2019-04-26 Moved napier sliders up by 1mm. Optimal visibility of numerals. Added a spring for the napier sliders. optional.
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2019-05-05 adder: writing on the wheel from green to blue. Do not laser. Ignore. That should save some time.
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2019-07-15 Adder Assembly Aids Carry Wheels: Front washers added, tolerances +0.1mm Thanks for noticing this, Jens.
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2019-11-10 sign 3d model
    [sign.FCStd]
2019-11-11 3d buildng blocks for adder done
    [adder_box.FCStd, adder_carry.FCStd, adder_wheels.FCStd]
2019-11-13 adder_box model done
    [adder_box.FCStd, adder_box.stl, adder_box2.stl]
2019-11-13 only the correct stl please.
    [adder_box.stl, adder_box2.stl]
2019-11-13 move stls to the stl folder
    [adder_box.stl]
2019-11-13 assembled carry wheels
    [adder_carry.FCStd, adder_wheels.FCStd]
2019-11-13 STLs of assembled carry wheels.
    [adder_carry.FCStd, adder_carry_A_C_E.stl, adder_carry_B_D.stl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]
2019-11-14 add spring assembly to adder box.
    [adder_box.FCStd, adder_box.stl]
2019-11-15 adder wheel_shafts assembled. Need to find the correct position for the wheels themselves now...
    [adder_wheels.FCStd, adder_wheels.stl]
2019-11-15 marked the back side of all adder wheels and adder carry wheels
    [adder_wheels.FCStd, adder_wheels.stl, adder_wheels_front_knob.stl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]
2019-11-17 walls erected. connectors still missing
    [side_walls.FCStd]
2019-11-17 side-walls modelled. Fixed a small offset bug on the side walls near the memory unit.
    [side_walls.FCStd, side_walls.stl]
2019-11-17 memory_box model done
    [memory_box.FCStd, side_walls.FCStd]
2019-11-18 added memory_wheels model
    [memory_box.FCStd, memory_wheel.stl, memory_wheels.FCStd]
2019-11-18 napier_box wip
    [napier_box.FCStd]
2019-11-18 napier_box stl objects done. Made the lid hooks and their notches in the front top 1mm shorter. Cosmetic change.
    [memory_box.FCStd, napier_blinds_pos_aid.stl, napier_box.FCStd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]
2019-11-19 napier drum stl done.
    [napier_drum.stl, napier_drums.FCStd]
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2020-01-20 made the adder spring freecad model show double rollers per arm.
    [adder_box.FCStd]
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2023-01-21 Hacked an assembly into adder_box, after wasting 3 hours trying Assembly 3 and Assembly 4 workbench. Both explode with funny error messages on me.
2023-04-10 added knob_assembly_positioning_aid
    [knob_assembly_positioning_aid.FCStd]
2023-04-27 screensots updated to show two 11mm rollers on each arm of adder spring
2023-04-27 Updated assembly guide to show two 11mm rollers on each arm of the adder spring.
2023-05-28 added first draft of sliding walls enhancement
    [napier_drums.FCStd]
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2025-02-26 scaling bug in schickard_3050_a1.svg fixed.
    The adder box was 2.8 mm too short. It should be 325mm wide, like the other boxes.
    This issue only exists here. The schickard_adder.svg file in the parent folder did not have this issue.
